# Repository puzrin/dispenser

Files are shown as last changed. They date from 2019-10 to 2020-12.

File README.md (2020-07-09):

SMT solder paste and flux dispenser
===================================




**WIP**

> Motorized dispenser for SMT boards soldering. Compact, cheap & easy to do.



Schematic & PCB:

- [EasyEDA project page](https://easyeda.com/puzrin/dispenser) - order PCB and
  all components in couple of clicks.

Project page on [hackaday.io](https://hackaday.io/project/166699-solder-paste-and-flux-dispenser).
See progress and other tips in build logs.

## Build & usage

- [Assembly guide](doc/assembly.md)
- [User manual](doc/manual.md)

If you plan to develop new features or create fixes - see
[Devolopment notes](doc/development.md).

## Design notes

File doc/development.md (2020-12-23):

Development notes<!-- omit in toc -->
=================

- [PC Simulator](#pc-simulator)
- [Messaging via USB Serial](#messaging-via-usb-serial)
- [Bare metal debug](#bare-metal-debug)

## PC Simulator

Firmware has simulator option for quick GUI development on desktop. It requires
SDL2 and was tested with Ubuntu 18.04LTS.

For dependencies install:

```sh
sudo apt-get install libsdl2-dev
```

To build & execute, via PlatformIO menu: `Terminal` -> `Run Build Task` ->
`PlatformIO: Execute (emulator)`.

## Messaging via USB Serial

Dispenser has built-in USB CDC descriptor with `stdout` retargeting. All
`printf()` output will be sent to virtual COM-port. By default, it sends
 LVGL memory pool usage info.

In linux, to see `tty` name of attached device type:

```sh
dmesg | grep tty
```

Then, to see messages, use:

```sh
screen /dev/<tty_name_from_dmesg>
```

For example: `screen /dev/ttyACM0`.

## Bare metal debug

In some cases you may wish to debug bare metal. PCB has SWD connector pins,
where to can attach ST-Link/V2. See PlatformIO docs for more details about
debugger.

We do not promote SWD connector in other documents, because for ordinary use USB
is enough and more simple.

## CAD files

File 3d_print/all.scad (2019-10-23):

e = 0.01;
2e = 0.02;

$fn = 128;

pcb_wide_w = 25;
pcb_wide_len = 40;
pcb_narrow_w = 15;
pcb_len = 120;

pcb_color = "Pink";


motor_dia = 15;
motor_len = 20;
motor_flange_len = 1; // shaft flange bearing outer
motor_shaft_len = 7;
motor_shaft_dia = 3;

motor_color = "RoyalBlue";

shaft_coupler_dia = 9;
shaft_coupler_len = 20;
shaft_coupler_offset = motor_len + motor_flange_len;

pusher_path_len = 35;

pusher_rod_len = pusher_path_len + 7;
pusher_rod_dia = 3;

pusher_len = pusher_path_len + 7;
pusher_dia = 11;

pusher_max_offset = motor_len + motor_flange_len + shaft_coupler_len + pusher_path_len + pusher_len;


////////////////////////////////////////////////////////////////////////////////
// Syringe sizes

s_medical_10cc = [
    20.4, // flange_h
    31.6, // flange_w
    16.5, // outer_dia
    14.5, // inner_dia
    75.3, // inner length
    6.5   // pusher head fatness
];

s_pneumo_10cc = [
    22.5, // flange_h
    34.1, // flange_w
    18.5, // outer_dia
    15.5,  // inner_dia
    75.3, // inner length
    2   // pusher head fatness
];

function s_flange_h(data) = data[0];
function s_flange_w(data) = data[1];
function s_outer_dia(data) = data[2];
function s_inner_dia(data) = data[3];
function s_body_len(data) = data[4];
function s_pusher_head(data) = data[5];
function s_axis_z(data) = s_flange_h(data) / 2;

function s_offset(data) = pusher_max_offset - s_body_len(data) + s_pusher_head(data);


////////////////////////////////////////////////////////////////////////////////
// Printed elements

module pusher() {
    //cylinder(pusher_len, d = pusher_dia);
    inner = 4/2 + 0.1;
    outer = pusher_dia/2;
    enforcer_h = 10;
    rounding = 0.5;
    gap_h = 15;
    
    f_ofs = 20;
    f_h = 3;
    
    //color("Red", 0.4)
    difference() {
        rotate_extrude()
        polygon([
            [ inner, 0 ],

            // stopper for metal enforcer insert
            [ inner, enforcer_h ],
            [ inner - 0.4, enforcer_h + 0.4 ],
            [ inner,  enforcer_h + 0.4 + 0.4 ],
        
            [ inner, pusher_len ],
            [ outer - rounding, pusher_len ],
            [ outer, pusher_len - rounding ],

            // Place for soft friction material
            [ outer, f_ofs +f_h + 0.5 ],
            [ outer - 0.5, f_ofs + f_h ],
            [ outer - 0.5, f_ofs ],
            [ outer, f_ofs - 0.5 ],


            [ outer, rounding ],
            [ outer - rounding, 0 ],
        ]);
        
        translate([ 0, 0, pusher_len - gap_h/2 + e ])
        cube([pusher_dia + e, 1, gap_h], center = true);

        rotate([ 0, 0, 90 ])
        translate([ 0, 0, pusher_len - gap_h/2 + e ])
        cube([pusher_dia + e, 1, gap_h], center = true);
    }
}

module motor_support(syringe) {
    space = (s_flange_h(syringe) - motor_dia) / 2;

    difference() {
        translate([ 0, -pcb_wide_w/2, 0 ])
        cube([ motor_len, pcb_wide_w, space * 2 ]);
        
        motor_body(syringe);
    }
}

module syringe_support(syringe) {
    space = (s_flange_h(syringe) - s_outer_dia(syringe)) / 2;
    support_len = 15;
    support_w = 10;

    difference() {
        translate([ 0, -support_w/2, 0 ])
        cube([support_len, support_w, space * 1.5]);
        
        translate([ -e, 0, s_flange_h(syringe)/2 ])
        rotate([0, 90, 0])
        cylinder(support_len + 2e,d = s_outer_dia(syringe));
    }
}

////////////////////////////////////////////////////////////////////////////////
// Virtual elements

module pcb() {
    smoothed_len = (pcb_wide_w - pcb_narrow_w) / 2;
    
    color(pcb_color, 0.5)
    translate([ 0, 0, -2 ])
    linear_extrude(1.6)
    difference() {
        polygon([
            [ 0, pcb_wide_w/2 ],
            [ pcb_wide_len, pcb_wide_w/2 ],
            [ pcb_wide_len + smoothed_len, pcb_narrow_w/2 ],
            [ pcb_len, pcb_narrow_w/2 ],
            [ pcb_len, -pcb_narrow_w/2 ],
            [ pcb_wide_len + smoothed_len, -pcb_narrow_w/2 ],
            [ pcb_wide_len, -pcb_wide_w/2 ],
            [ 0, -pcb_wide_w/2 ]    
        ]);
        
        translate([ 51, 0, 0 ]) {
            ofs = pcb_narrow_w / 2;

            translate([ 0, ofs, 0]) circle(d = 3);
            translate([ 0, -ofs, 0]) circle(d = 3);
            translate([ 6, ofs, 0]) circle(d = 3);
            translate([ 6, -ofs, 0]) circle(d = 3);
        }
    }
}


module motor_body(syringe) {
    z_level = s_axis_z(syringe);

    translate([ 0, 0, z_level])
    rotate([0, 90, 0])
    translate([ 0, 0, -e ])
    cylinder(motor_len + 2e, d = motor_dia);
}

module motor(syringe) {
    z_level = s_axis_z(syringe);

    color(motor_color, 0.6)
    motor_body(syringe);

    translate([ 0, 0, z_level])
    rotate([0, 90, 0]) {
        color(motor_color)
        cylinder(motor_len + motor_shaft_len, d = motor_shaft_dia);
    }
}


module pusher_model(syringe) {
    z_level = s_axis_z(syringe);
    
    translate([ shaft_coupler_offset, 0, z_level])
    rotate([0, 90, 0]) {
        // Coupling
        color("SeaGreen", 0.7)
        cylinder(shaft_coupler_len, d = shaft_coupler_dia);

        // Pusher shaft
        color(motor_color, 0.5)
        translate([ 0, 0, shaft_coupler_len/2 ])
        cylinder(pusher_rod_len + shaft_coupler_len/2, d = pusher_rod_dia);
        
        // Working body
        translate([ 0, 0, shaft_coupler_len + pusher_path_len ])
        pusher();
    }
}

module syringe_body(syringe) {
    h = s_body_len(syringe) + 1;
    z_level = s_axis_z(syringe);

    color("Azure", 0.4)
    translate([
        s_offset(syringe),
        0,
        z_level
    ])
    rotate([0, 90, 0])
    difference() {
        union() {
            cylinder(h, d = s_outer_dia(syringe));
            
            translate([ 0, 0, 0.5 ])
            cube([
                s_flange_h(syringe),
                s_flange_w(syringe),
                1
            ], center = true);
            
            translate([ 0, 0, h - e ]) {
                cylinder(9.5, d = 8);
                cylinder(11.5, d = 4);
            }
        };
        
        translate([ 0, 0, -e ])
        cylinder(h - 1, d = s_inner_dia(syringe));
    }
}

////////////////////////////////////////////////////////////////////////////////

syringe = s_medical_10cc;
//syringe = s_pneumo_10cc;

print = true;

if (print == false) {
    pcb();
    
    translate([ 0, 0, 1 ]) {
        motor(syringe);
        pusher_model(syringe);
        syringe_body(syringe);
    }

    motor_support(syringe);

    translate([ 52, 0, 0])
    syringe_support(syringe);

    translate([ 103, 0, 0])
    syringe_support(syringe);
} else {
    pusher();

    translate([ 10, 0, 0])
    motor_support(syringe);

    translate([ 35, 0, 0])
    syringe_support(syringe);

    translate([ 55, 0, 0])
    syringe_support(syringe);
}

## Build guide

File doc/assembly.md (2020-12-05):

Device assembly <!-- omit in toc -->
===============

- [Required components](#required-components)
- [PCB assembly](#pcb-assembly)
- [Firmware upload](#firmware-upload)
- [Motor & syringe mount](#motor--syringe-mount)
- [Needle caps](#needle-caps)
- [The end :)](#the-end-)

## Required components

This dispenser is inexpensive and small, expected to be used without syringe replace. Consider build separate one for each substance you plan to use (normal
paste, low temp paste, flux).

&nbsp; | Name | Comment
-----|-------------|--------
1 | [PCB & Components](https://easyeda.com/puzrin/dispenser) | Go to EasyEda project page and order both in couple of clicks. If you order PCB first, components second, then you will be able to join delivery and save some bucks. SMT stencil strongly advised, see note below.
2 | [0.96" IPS Display](https://www.aliexpress.com/item/32861823719.html) |
3 | [Micro stepper motor](https://www.aliexpress.com/item/32979960185.html) | Other motors will need rework of 3d-printed supports.
4 | [Gearbox 1:300+ with long shaft](https://www.aliexpress.com/item/32987637967.html) | For max gear ratio select lowest RPM.
5 | [PVC transparent heat shrink tube 23mm](https://aliexpress.ru/item/32787322976.html) | Display mount.
6 | [Double side foam tape, 15*1mm](https://www.aliexpress.com/item/33050888785.html) | Display mount.
6 | [22 AWG wire](https://www.aliexpress.com/item/32854919883.html) | SMT stencil positioning & motor/syringe supports mount.
7 | [Heat shrink tube 35mm](https://www.aliexpress.com/item/32791427710.html) | Motor mount / electronics protection.
8 | [Cable ties 150-200mm](https://www.aliexpress.com/item/32807062474.html) | Syringe mount. 100mm enough for all syringes except 10cc. Width 2.5-3.0mm.
9 | [Silicone heat shrink tube 0.8mm, 1.0mm, 1.5mm](https://atopelec.aliexpress.com/store/group/Silicone-Heat-Shrink-Tubing/118669_505069419.html) | Needle caps, inner layer.
10 | [Heat shrink tube 1:4 with glue, 4mm](https://www.aliexpress.com/item/32787521306.html) | Needle caps, outer layer.
11 | [Joysick cap, 2mm](https://www.aliexpress.com/item/4000005913318.html) | Optional, but recommended.
12 | [Syringes](https://www.aliexpress.com/item/32920861566.html) | 1cc recommended for soldering paste with max precision. 3cc - acceptable. 10cc - for fluxes when precision not critical, and for refill.
13 | [Needles](https://www.aliexpress.com/item/32256297497.html) | Needles choice from syringe set is too small. Buy separate set.
14 | [Micro USB silicon cable](https://www.aliexpress.com/item/32858516897.html) | Very soft cable strongly advised for convenience.

Note. You are strongly advised to order SMT stencil for your PCB. That will
add ~ 8$ in total to your order - good price for convenience. On placing stencil
order at jlcpcb, select option "custom size", and define 30*130mm. Then stencil
will be compact and light, with small delivery cost. You need top layer only. If
you order SMT stencil, add this comment:

_"Please make stencil with my paste layer directly. Make sure 2 TP rounds 0.7mm
with X = 43.0 and X = 108.0 exist"_

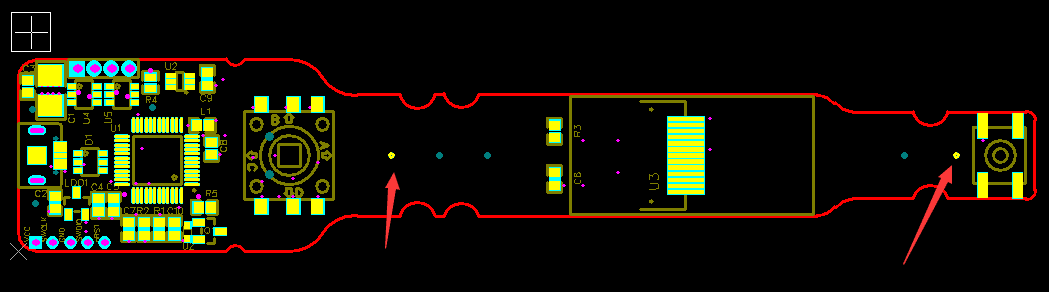
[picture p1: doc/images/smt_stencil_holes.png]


## PCB assembly

This sequence is for assembly with heat gun:

- Solder everything except buttons and LCD.
- Solder buttons manually.
- Wash PCB from flux.
- Solder LCD.
- Use IPA to accurately clean LCD soldering area. Or leave as is, if
  your flux is no-clean.

Warning. DON'T USE STRONG CLEANERS WITH LCD. It's not sealed, assembled with
soft glue and will be damaged. That's why it's better to install it in last
moment - you can clean PCB anyhow, but use IPA only with LCD.

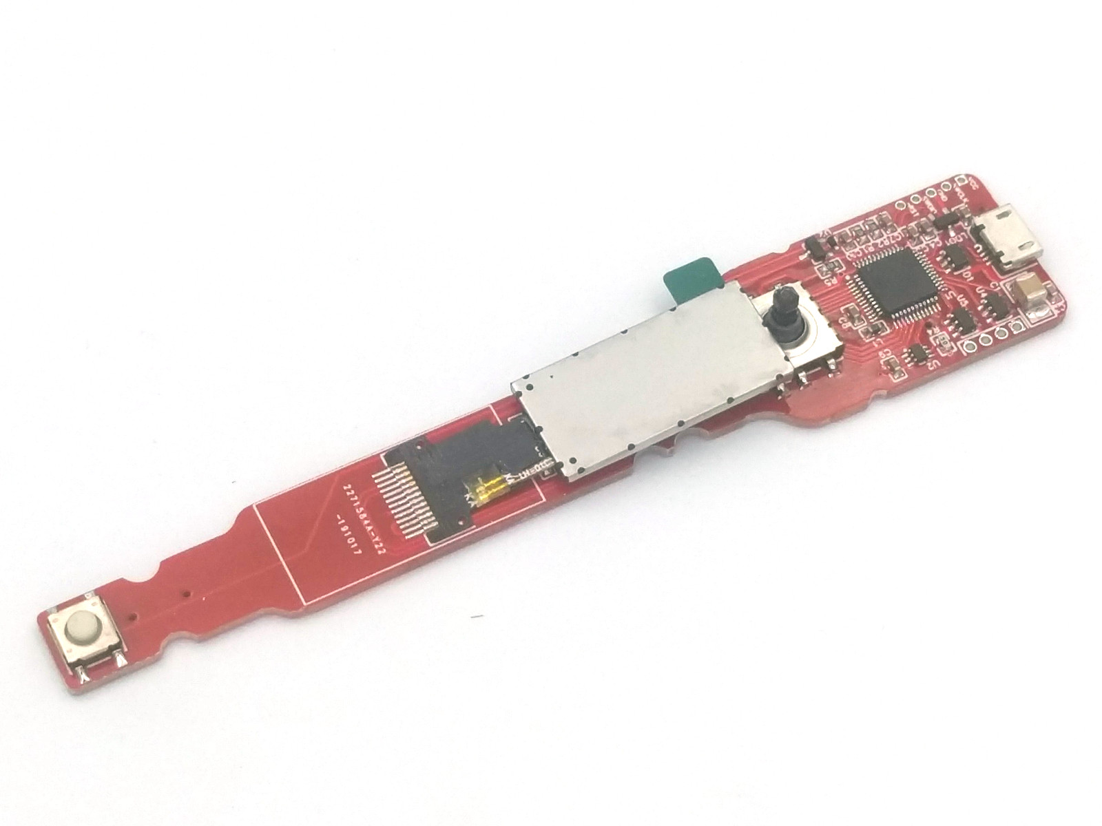
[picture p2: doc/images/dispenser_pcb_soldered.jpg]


Note. _Here it's good idea to upload firmware and check display works, prior to
continue (see instructions in next chapter)_.

Now mount LCD to PCB:

- Use double side foam tape. Stick to LCD first, then cut borders, then stick
  to PCB
- Fit heat shrink tube over that. You need 40mm of 23mm-wide tube. Center it
  over LCD, then shrink sides, front and back.

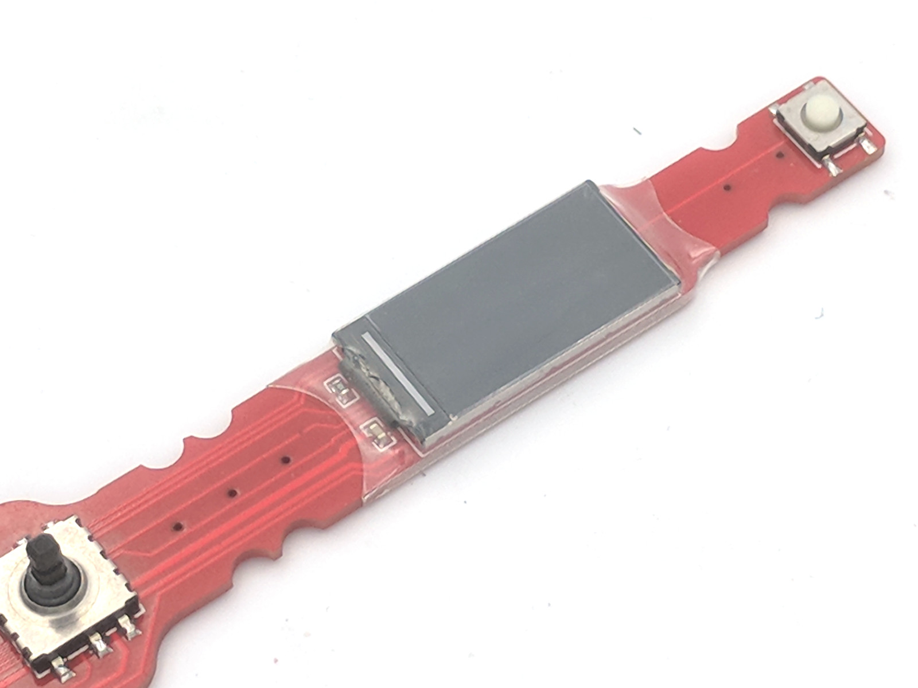
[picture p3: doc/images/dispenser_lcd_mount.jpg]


Don't worry about small air bubbles at screen surface, those will not affect
image quality anyhow. It's possible to use special UV-activated glue for
displays to avoid air gaps. But that does not worth efforts been spent.

Assembled PCB with power on:

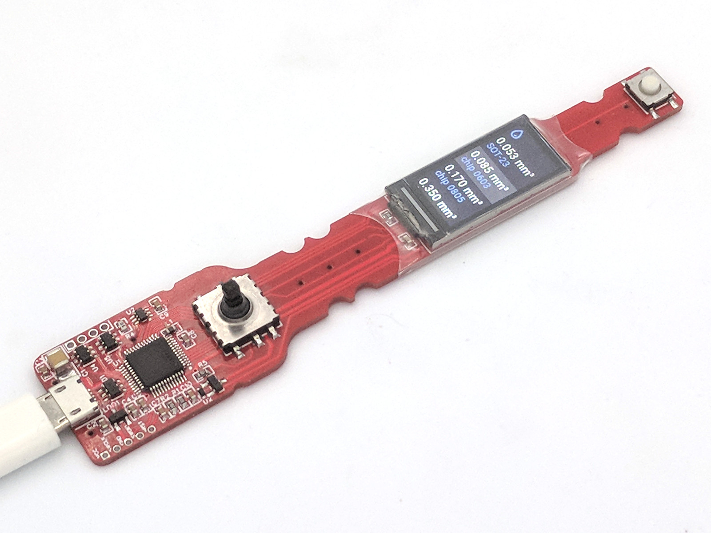
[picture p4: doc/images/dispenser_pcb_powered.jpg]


## Firmware upload

You need VS Code to build and upload firmware. It's our choice, because
it works on all operating systems and requires almost zero efforts to configure.

1. Install [VS Code](https://code.visualstudio.com/). Then configure hardware if
   needed:
   - For Linux, add [udev rules](http://docs.platformio.org/en/latest/installation.html#troubleshooting)
2. Clone this repo or download as zip archive and unpack somewhere.
3. Open folder in VS Code AND after it suggests to install plugins - agree
   with everything. That should install PlatformIO and all required dependencies.

How to flash:

1. Push joystick button and attach USB cable. It's important to push joystick
   before cable attached, to put device in programming mode.
2. In VS Code menu select `Terminal` -> `Run task` -> `PlatformIO: Upload (hardware_usb)`
   and wait until succeed.
3. Re-insert USB cable. You should see dispenser menu on display.

## Motor & syringe mount

TBD

## Needle caps

It's important to protect soldering paste from drying while not used. Here is
simple recipe of needle caps. You will need 2 heat shrink tubes:

- Small silicone tube. They have small shrink ratio (1.7:1 only), so buy several
  sizes to fit all 0.8/1.0/1.5mm.
- Bigger tube, 4mm, with glue layer & 1:4 ratio.

First, shrink 10mm of silicone tube at needle edge. Then shrink 15-20mm of
bigger tube and squeeze the end. Take off and cut the ends for accurate look.
See result:

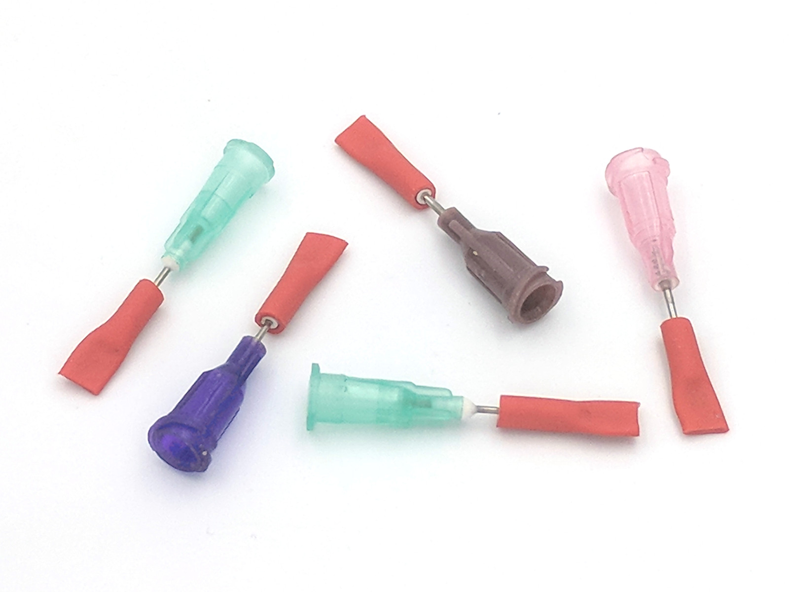
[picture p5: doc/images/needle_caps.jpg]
Needle caps


## The end :)

When dispenser ready, follow to [User Manual](./manual.md).

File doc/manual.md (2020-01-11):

User Manual <!-- omit in toc -->
===========

- [Control](#control)
- [Settings](#settings)
- [Viscosity](#viscosity)
- [Syringe refill](#syringe-refill)

Dispenser works in 2 modes - dose and flow. In dose, it dispense fixed portions
on each press. In flow mode, it continue dispense until button pressed.

Dose volume and dispense speed are selectable.

## Control

Joystick:

- Short push - mode switch (portion/flow).
- Long push - goto settings.
- Up/Down - move selection.
- Left/Right - change value (settings only).

You can edit `src/doses.cpp` file to change list of selectable portions.

## Settings

This params are used to estimate optimal dispense speed and portion volumes.

- **Syringe dia** - inner diameter of syringe. Required to properly calculate
  portion sizes. If you plan to dispense very small doses (0603 and below), we
  recommend to use smallest possible syringe (1cc).
- **Viscosity** - defines dispense speed and retract size. Typical values are
  described in next chapter.
- **Flux volume** - % of flux in paste. Needed to calculate proper volume of
  solder. If you need to dispence glues or fluxes - set to zero.
- **Fast move** - quick move pusher back and forward for syringe refill.

## Viscosity

Viscosity depend very much on temperature. Table below contain only average
value for room env.

_cP = centipoise = 0.1 Pa·s (pascal-second) = mPa·s_

Substance | Viscosity (cP)
----------|---------------
Soldering paste for SMT stencil | 650K-1200K
Soldering paste for dispenser | 300K-450K
Glycerol | 1400
Water | 1

## Syringe refill

Everything is done without disassembly. You will need only additional syringe
and luer coupler.

Notes:

- It's important to fill syringe without air bubbles.
- Avoid buy paste in syringes, because it can have air bubbles with very high
  probability. Prefer flasks.

Steps:

1. Fill helper (charger) syringe with paste. You can do that in different ways:
   - As on this video.
2. Move dispenser's pusher back via settings menu.
3. Attach needle to charger and fill dispenser's nozzle to leave no air.
4. Change needle to luer coupler and make sure i't filled with paste.
   Fill coupler before attach
5. Attach another end of coupler to dispenser and fill it.
6. Attach needle with protective cap to dispenser.

Tips:

- You can heat paste to 40-50C in hot water, to make it more liquid. But don't
  heat it too much and too long, because it can stratify.
- You can experiment with adding some flux to make old paste more liquid. But
  consider just buy paste in smaller packaging and use new one :). Paste is
  cheap, don't search difficulties to save couple of bucks.

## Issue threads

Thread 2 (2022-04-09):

Major bug in your source code!

heyrussia, 2022-04-09:
Привет @puzrin из StPetersburg.
Может быть, вы проснулись сегодня утром счастливым, как обычно, не особо задумываясь о жизни.
К сожалению, я должен лишить вас этого прекрасного дня.
Потому что вы были выбраны нами для великой задачи.

Украина уже больше месяца находится в состоянии войны.
Правительство России  вторглось в Украину, без согласия граждан. Ваши сыновья, мужья и просто знакомые погибают и становятся калеками, на войне, которая нужна лишь Путину.

**Но вы можете что-то изменить.**

Выполните следующие шаги, чтобы безопасно присоединиться к Сопротивлению и работать с другими, чтобы изменить историю к лучшему:

1. Установите бесплатный VPN-клиент на свой компьютер или смартфон.
2. Загрузите браузер Tor [https://www.torproject.org/](https://www.torproject.org/)
3. Присоединяйтесь к Матричному серверу Сопротивления. [https://matrix.to/#/#resistance-against-the-government:matrix.org](https://matrix.to/#/#resistance-against-the-government:matrix.org)
4. Найдите свои группы и организуйте сопротивление
5. Поделитесь этим сообщением со своими близкими друзьями и семьей или анонимно в Интернете.

---

Hello @puzrin from StPetersburg.

Maybe you woke up this morning happy as usual, without thinking much about life.
Unfortunately, I have to distract you from this beautiful day.
Because **you** have been chosen by us for a great task.

Ukraine has been at war for over a month.
The Russian government has invaded Ukraine without informing the citizens.
Your sons, husbands and just acquaintances are dying and becoming crippled in a war that only Putin needs.
Now everyone involved is suffering greatly from the consequences of this attack.

**But you can change something.**

Follow these steps to safely join the Resistance and work with others to change history for the better:

1. Install a free VPN client on your computer or smartphone.
2. Download the Tor Browser [https://www.torproject.org/](https://www.torproject.org/)
3. Join the Matrix Server of the Resistance [https://matrix.to/#/#resistance-against-the-government:matrix.org](https://matrix.to/#/#resistance-against-the-government:matrix.org)
4. Find your groups and organize the resistance
5. Share this message with your close friends and family or anonymously on the web

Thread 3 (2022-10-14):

Solder paste and flux dispenser

crazoff, 2022-10-14:
Здравствуйте Виталий. Заинтересовал паш проект https://hackaday.io/project/166699-solder-paste-and-flux-dispenser Решил повторить, но возникли трудности со скачиванием прошивки микроконтроллера. Я использовал Visual Studio Code, при заполнении которого выдается следующее сообщение.

* Выполнение задачи: C:\Users\Crazoff\.platformio\penv\Scripts\platformio.exe run --target upload

Предупреждение! Параметр конфигурации `src_build_flags` в разделе [env:emulator] устарел и будет удален в следующем выпуске! Вместо этого используйте `build_src_flags`
Предупреждение! Параметр конфигурации `src_filter` в разделе [env:emulator] устарел и будет удален в следующем выпуске! Вместо этого используйте `build_src_filter`
Предупреждение! Параметр конфигурации `src_filter` в разделе [env:hardware_stlink] устарел и будет удален в следующем выпуске! Вместо этого используйте `build_src_filter`
Эмулятор обработки (платформа: родная)
-------------------------------------------------- ------------------------------
Подробный режим можно включить с помощью опции `-v, --verbose`
LDF: поиск зависимостей библиотеки -> https://bit.ly/configure-pio-ldf
Режимы LDF: Finder ~ цепочка, Совместимость ~ soft
Диспетчер библиотек: установка библиотеки встроенных шаблонов @ ~18.3.2
Предупреждение! Не удалось найти пакет с требованиями «Встроенная библиотека шаблонов @ ~ 18.3.2» для вашей системы «windows_amd64».
Найдено 2 совместимые библиотеки
Сканирование зависимостей...
График зависимости
|-- лвгл @ 6.1.1
|-- lv_drivers @ 6.1.1
| |-- лвгл @ 6.1.1
Сборка в релизном режиме
Компиляция .pio\build\emulator\hal\sdl2\app_hal.o
"g++" \xad\xa5 \xef\xa5\xe2\xe1\xef \xa2\xad\xe3\xe2७\xad\xa5\xa9 \xa8\xab\xa8 \xa2\xad\xa5譥\xa9
\xaa\xae\xac\xa0\xad\xa4\xae\xa9, \xa8ᯮ\xab\xad塞\xae\xa9 \xafணࠬ\xac\xae\xa9 \xaa8\xab\xa8 \xaf\xa0\xaa\xa5 \xe2\xad\xeb\xac 䠩\xab\xae\xac.
Компиляция .pio\build\emulator\src\app.o
Компиляция .pio\build\emulator\src\doses.o
"g++" \xad\xa5 \xef\xa5\xe2\xe1\xef \xa2\xad\xe3\xe2७\xad\xa5\xa9 \xa8\xab\xa8 \xa2\xad\xa5譥\xa9
\xaa\xae\xac\xa0\xad\xa4\xae\xa9, \xa8ᯮ\xab\xad塞\xae\xa9 \xafணࠬ\xac\xae\xa9 \xaa8\xab\xa8 \xaf\xa0\xaa\xa5 \xe2\xad\xeb\xac 䠩\xab\xae\xac.
Компиляция .pio\build\emulator\src\fonts\my_font_icons_18.o
"g++" \xad\xa5 \xef\xa5\xe2\xe1\xef \xa2\xad\xe3\xe2७\xad\xa5\xa9 \xa8\xab\xa8 \xa2\xad\xa5譥\xa9
\xaa\xae\xac\xa0\xad\xa4\xae\xa9, \xa8ᯮ\xab\xad塞\xae\xa9 \xafணࠬ\xac\xae\xa9 \xaa8\xab\xa8 \xaf\xa0\xaa\xa5 \xe2\xad\xeb\xac 䠩\xab\xae\xac.
Компиляция .pio\build\emulator\src\fonts\my_font_roboto_12.o
"gcc" \xad\xa5 \xef\xa5\xe2\xe1\xef \xa2\xad\xe3\xe2७\xad\xa5\xa9 \xa8\xab\xa8 \xa2\xad\xa5譥\xa9
\xaa\xae\xac\xa0\xad\xa4\xae\xa9, \xa8ᯮ\xab\xad塞\xae\xa9 \xafணࠬ\xac\xae\xa9 \xaa8\xab\xa8 \xaf\xa0\xaa\xa5 \xe2\xad\xeb\xac 䠩\xab\xae\xac.
Компиляция .pio\build\emulator\src\fonts\my_font_roboto_14.o
"gcc" \xad\xa5 \xef\xa5\xe2\xe1\xef \xa2\xad\xe3\xe2७\xad\xa5\xa9 \xa8\xab\xa8 \xa2\xad\xa5譥\xa9
\xaa\xae\xac\xa0\xad\xa4\xae\xa9, \xa8ᯮ\xab\xad塞\xae\xa9 \xafணࠬ\xac\xae\xa9 \xaa8\xab\xa8 \xaf\xa0\xaa\xa5 \xe2\xad\xeb\xac 䠩\xab\xae\xac.
Компиляция .pio\build\emulator\src\fonts\my_font_roboto_num_18.o
"gcc" \xad\xa5 \xef\xa5\xe2\xe1\xef \xa2\xad\xe3\xe2७\xad\xa5\xa9 \xa8\xab\xa8 \xa2\xad\xa5譥\xa9
\xaa\xae\xac\xa0\xad\xa4\xae\xa9, \xa8ᯮ\xab\xad塞\xae\xa9 \xafணࠬ\xac\xae\xa9 \xaa8\xab\xa8 \xaf\xa0\xaa\xa5 \xe2\xad\xeb\xac 䠩\xab\xae\xac.
Компиляция .pio\build\emulator\src\screen_dose.o
"gcc" \xad\xa5 \xef\xa5\xe2\xe1\xef \xa2\xad\xe3\xe2७\xad\xa5\xa9 \xa8\xab\xa8 \xa2\xad\xa5譥\xa9
\xaa\xae\xac\xa0\xad\xa4\xae\xa9, \xa8ᯮ\xab\xad塞\xae\xa9 \xafணࠬ\xac\xae\xa9 \xaa8\xab\xa8 \xaf\xa0\xaa\xa5 \xe2\xad\xeb\xac 䠩\xab\xae\xac.
Компиляция .pio\build\emulator\src\screen_flow.o
"g++" \xad\xa5 \xef\xa5\xe2\xe1\xef \xa2\xad\xe3\xe2७\xad\xa5\xa9 \xa8\xab\xa8 \xa2\xad\xa5譥\xa9
\xaa\xae\xac\xa0\xad\xa4\xae\xa9, \xa8ᯮ\xab\xad塞\xae\xa9 \xafணࠬ\xac\xae\xa9 \xaa8\xab\xa8 \xaf\xa0\xaa\xa5 \xe2\xad\xeb\xac 䠩\xab\xae\xac.
Компиляция .pio\build\emulator\src\screen_settings.o
"g++" \xad\xa5 \xef\xa5\xe2\xe1\xef \xa2\xad\xe3\xe2७\xad\xa5\xa9 \xa8\xab\xa8 \xa2\xad\xa5譥\xa9
\xaa\xae\xac\xa0\xad\xa4\xae\xa9, \xa8ᯮ\xab\xad塞\xae\xa9 \xafணࠬ\xac\xae\xa9 \xaa8\xab\xa8 \xaf\xa0\xaa\xa5 \xe2\xad\xeb\xac 䠩\xab\xae\xac.
"g++" \xad\xa5 \xef\xa5\xe2\xe1\xef \xa2\xad\xe3\xe2७\xad\xa5\xa9 \xa8\xab\xa8 \xa2\xad\xa5譥\xa9
\xaa\xae\xac\xa0\xad\xa4\xae\xa9, \xa8ᯮ\xab\xad塞\xae\xa9 \xafணࠬ\xac\xae\xa9 \xaa8\xab\xa8 \xaf\xa0\xaa\xa5 \xe2\xad\xeb\xac 䠩\xab\xae\xac.
Компиляция .pio\build\emulator\libc67\lvgl\lv_core\lv_debug.o
Компиляция .pio\build\emulator\libc67\lvgl\lv_core\lv_disp.o
*** [.pio\build\emulator\hal\sdl2\app_hal.o] Ошибка 1
*** [.pio\build\emulator\src\app.o] Ошибка 1
*** [.pio\build\emulator\src\doses.o] Ошибка 1
*** [.pio\build\emulator\src\fonts\my_font_icons_18.o] Ошибка 1
*** [.pio\build\emulator\src\fonts\my_font_roboto_12.o] Ошибка 1
*** [.pio\build\emulator\src\fonts\my_font_roboto_14.o] Ошибка 1
*** [.pio\build\emulator\src\fonts\my_font_roboto_num_18.o] Ошибка 1
*** [.pio\build\emulator\src\screen_dose.o] Ошибка 1
*** [.pio\build\emulator\src\screen_flow.o] Ошибка 1
*** [.pio\build\emulator\src\screen_settings.o] Ошибка 1
"gcc" \xad\xa5 \xef\xa5\xe2\xe1\xef \xa2\xad\xe3\xe2७\xad\xa5\xa9 \xa8\xab\xa8 \xa2\xad\xa5譥\xa9
\xaa\xae\xac\xa0\xad\xa4\xae\xa9, \xa8ᯮ\xab\xad塞\xae\xa9 \xafணࠬ\xac\xae\xa9 \xaa8\xab\xa8 \xaf\xa0\xaa\xa5 \xe2\xad\xeb\xac 䠩\xab\xae\xac.
*** [.pio\build\emulator\libc67\lvgl\lv_core\lv_debug.o] Ошибка 1
"gcc" \xad\xa5 \xef\xa5\xe2\xe1\xef \xa2\xad\xe3\xe2७\xad\xa5\xa9 \xa8\xab\xa8 \xa2\xad\xa5譥\xa9
\xaa\xae\xac\xa0\xad\xa4\xae\xa9, \xa8ᯮ\xab\xad塞\xae\xa9 \xafணࠬ\xac\xae\xa9 \xaa8\xab\xa8 \xaf\xa0\xaa\xa5 \xe2\xad\xeb\xac 䠩\xab\xae\xac.
*** [.pio\build\emulator\libc67\lvgl\lv_core\lv_disp.o] Ошибка 1
========================== [FAILED] Заняло 4,17 секунды =================== ========

Продолжительность состояния окружающей среды
------------- -------- ------------
эмулятор ОШИБКА 00:00:04.174
==================== 1 сбой, 0 успешно в 00:00:04.174 =================== знак равно

* Терминальный процесс "C:\Users\Crazoff\.platformio\penv\Scripts\platformio.exe 'run', '--target', 'upload'" завершился кодом выхода: 1.
* Терминал будет повторно использоваться задачами, нажмите любую клавишу, чтобы закрыть его.

* Выполнение задачи: C:\Users\Crazoff\.platformio\penv\Scripts\platformio.exe run --target upload

Предупреждение! Параметр конфигурации `src_build_flags` в разделе [env:emulator] устарел и будет удален в следующем выпуске! Вместо этого используйте `build_src_flags`
Предупреждение! Параметр конфигурации `src_filter` в разделе [env:emulator] устарел и будет удален в следующем выпуске! Вместо этого используйте `build_src_filter`
Предупреждение! Параметр конфигурации `src_filter` в разделе [env:hardware_stlink] устарел и будет удален в следующем выпуске! Вместо этого используйте `build_src_filter`
Эмулятор обработки (платформа: родная)
-------------------------------------------------- ------------------------------
Подробный режим можно включить с помощью опции `-v, --verbose`
LDF: поиск зависимостей библиотеки -> https://bit.ly/configure-pio-ldf
Режимы LDF: Finder ~ цепочка, Совместимость ~ soft
Диспетчер библиотек: установка библиотеки встроенных шаблонов @ ~18.3.2
Предупреждение! Не удалось найти пакет с требованиями «Встроенная библиотека шаблонов @ ~ 18.3.2» для вашей системы «windows_amd64».
Найдено 2 совместимые библиотеки
Сканирование зависимостей...
График зависимости
|-- лвгл @ 6.1.1
|-- lv_drivers @ 6.1.1
| |-- лвгл @ 6.1.1
Сборка в релизном режиме
Компиляция .pio\build\emulator\hal\sdl2\app_hal.o
"g++" \xad\xa5 \xef\xa5\xe2\xe1\xef \xa2\xad\xe3\xe2७\xad\xa5\xa9 \xa8\xab\xa8 \xa2\xad\xa5譥\xa9
\xaa\xae\xac\xa0\xad\xa4\xae\xa9, \xa8ᯮ\xab\xad塞\xae\xa9 \xafணࠬ\xac\xae\xa9 \xaa8\xab\xa8 \xaf\xa0\xaa\xa5 \xe2\xad\xeb\xac 䠩\xab\xae\xac.
Компиляция .pio\build\emulator\src\app.o
Компиляция .pio\build\emulator\src\doses.o
"g++" \xad\xa5 \xef\xa5\xe2\xe1\xef \xa2\xad\xe3\xe2७\xad\xa5\xa9 \xa8\xab\xa8 \xa2\xad\xa5譥\xa9
\xaa\xae\xac\xa0\xad\xa4\xae\xa9, \xa8ᯮ\xab\xad塞\xae\xa9 \xafணࠬ\xac\xae\xa9 \xaa8\xab\xa8 \xaf\xa0\xaa\xa5 \xe2\xad\xeb\xac 䠩\xab\xae\xac.
Компиляция .pio\build\emulator\src\fonts\my_font_icons_18.o
"g++" \xad\xa5 \xef\xa5\xe2\xe1\xef \xa2\xad\xe3\xe2७\xad\xa5\xa9 \xa8\xab\xa8 \xa2\xad\xa5譥\xa9
\xaa\xae\xac\xa0\xad\xa4\xae\xa9, \xa8ᯮ\xab\xad塞\xae\xa9 \xafணࠬ\xac\xae\xa9 \xaa8\xab\xa8 \xaf\xa0\xaa\xa5 \xe2\xad\xeb\xac 䠩\xab\xae\xac.
Компиляция .pio\build\emulator\src\fonts\my_font_roboto_12.o
"gcc" \xad\xa5 \xef\xa5\xe2\xe1\xef \xa2\xad\xe3\xe2७\xad\xa5\xa9 \xa8\xab\xa8 \xa2\xad\xa5譥\xa9
\xaa\xae\xac\xa0\xad\xa4\xae\xa9, \xa8ᯮ\xab\xad塞\xae\xa9 \xafணࠬ\xac\xae\xa9 \xaa8\xab\xa8 \xaf\xa0\xaa\xa5 \xe2\xad\xeb\xac 䠩\xab\xae\xac.
Компиляция .pio\build\emulator\src\fonts\my_font_roboto_14.o
"gcc" \xad\xa5 \xef\xa5\xe2\xe1\xef \xa2\xad\xe3\xe2७\xad\xa5\xa9 \xa8\xab\xa8 \xa2\xad\xa5譥\xa9
\xaa\xae\xac\xa0\xad\xa4\xae\xa9, \xa8ᯮ\xab\xad塞\xae\xa9 \xafணࠬ\xac\xae\xa9 \xaa8\xab\xa8 \xaf\xa0\xaa\xa5 \xe2\xad\xeb\xac 䠩\xab\xae\xac.
Компиляция .pio\build\emulator\src\fonts\my_font_roboto_num_18.o
"gcc" \xad\xa5 \xef\xa5\xe2\xe1\xef \xa2\xad\xe3\xe2७\xad\xa5\xa9 \xa8\xab\xa8 \xa2\xad\xa5譥\xa9
\xaa\xae\xac\xa0\xad\xa4\xae\xa9, \xa8ᯮ\xab\xad塞\xae\xa9 \xafணࠬ\xac\xae\xa9 \xaa8\xab\xa8 \xaf\xa0\xaa\xa5 \xe2\xad\xeb\xac 䠩\xab\xae\xac.
Компиляция .pio\build\emulator\src\screen_dose.o
"gcc" \xad\xa5 \xef\xa5\xe2\xe1\xef \xa2\xad\xe3\xe2७\xad\xa5\xa9 \xa8\xab\xa8 \xa2\xad\xa5譥\xa9
\xaa\xae\xac\xa0\xad\xa4\xae\xa9, \xa8ᯮ\xab\xad塞\xae\xa9 \xafணࠬ\xac\xae\xa9 \xaa8\xab\xa8 \xaf\xa0\xaa\xa5 \xe2\xad\xeb\xac 䠩\xab\xae\xac.
"g++" \xad\xa5 \xef\xa5\xe2\xe1\xef \xa2\xad\xe3\xe2७\xad\xa5\xa9 \xa8\xab\xa8 \xa2\xad\xa5譥\xa9
Компиляция .pio\build\emulator\src\screen_flow.o
\xaa\xae\xac\xa0\xad\xa4\xae\xa9, \xa8ᯮ\xab\xad塞\xae\xa9 \xafணࠬ\xac\xae\xa9 \xaa8\xab\xa8 \xaf\xa0\xaa\xa5 \xe2\xad\xeb\xac 䠩\xab\xae\xac.
Компиляция .pio\build\emulator\src\screen_settings.o
"g++" \xad\xa5 \xef\xa5\xe2\xe1\xef \xa2\xad\xe3\xe2७\xad\xa5\xa9 \xa8\xab\xa8 \xa2\xad\xa5譥\xa9
\xaa\xae\xac\xa0\xad\xa4\xae\xa9, \xa8ᯮ\xab\xad塞\xae\xa9 \xafணࠬ\xac\xae\xa9 \xaa8\xab\xa8 \xaf\xa0\xaa\xa5 \xe2\xad\xeb\xac 䠩\xab\xae\xac.
"g++" \xad\xa5 \xef\xa5\xe2\xe1\xef \xa2\xad\xe3\xe2७\xad\xa5\xa9 \xa8\xab\xa8 \xa2\xad\xa5譥\xa9
\xaa\xae\xac\xa0\xad\xa4\xae\xa9, \xa8ᯮ\xab\xad塞\xae\xa9 \xafணࠬ\xac\xae\xa9 \xaa8\xab\xa8 \xaf\xa0\xaa\xa5 \xe2\xad\xeb\xac 䠩\xab\xae\xac.
Компиляция .pio\build\emulator\libc67\lvgl\lv_core\lv_debug.o
Компиляция .pio\build\emulator\libc67\lvgl\lv_core\lv_disp.o
*** [.pio\build\emulator\hal\sdl2\app_hal.o] Ошибка 1
*** [.pio\build\emulator\src\app.o] Ошибка 1
*** [.pio\build\emulator\src\doses.o] Ошибка 1
*** [.pio\build\emulator\src\fonts\my_font_icons_18.o] Ошибка 1
*** [.pio\build\emulator\src\fonts\my_font_roboto_12.o] Ошибка 1
*** [.pio\build\emulator\src\fonts\my_font_roboto_14.o] Ошибка 1
*** [.pio\build\emulator\src\fonts\my_font_roboto_num_18.o] Ошибка 1
*** [.pio\build\emulator\src\screen_dose.o] Ошибка 1
*** [.pio\build\emulator\src\screen_flow.o] Ошибка 1
*** [.pio\build\emulator\src\screen_settings.o] Ошибка 1
"gcc" \xad\xa5 \xef\xa5\xe2\xe1\xef \xa2\xad\xe3\xe2७\xad\xa5\xa9 \xa8\xab\xa8 \xa2\xad\xa5譥\xa9
\xaa\xae\xac\xa0\xad\xa4\xae\xa9, \xa8ᯮ\xab\xad塞\xae\xa9 \xafணࠬ\xac\xae\xa9 \xaa8\xab\xa8 \xaf\xa0\xaa\xa5 \xe2\xad\xeb\xac 䠩\xab\xae\xac.
*** [.pio\build\emulator\libc67\lvgl\lv_core\lv_debug.o] Ошибка 1
"gcc" \xad\xa5 \xef\xa5\xe2\xe1\xef \xa2\xad\xe3\xe2७\xad\xa5\xa9 \xa8\xab\xa8 \xa2\xad\xa5譥\xa9
\xaa\xae\xac\xa0\xad\xa4\xae\xa9, \xa8ᯮ\xab\xad塞\xae\xa9 \xafணࠬ\xac\xae\xa9 \xaa8\xab\xa8 \xaf\xa0\xaa\xa5 \xe2\xad\xeb\xac 䠩\xab\xae\xac.
*** [.pio\build\emulator\libc67\lvgl\lv_core\lv_disp.o] Ошибка 1
========================== [FAILED] Заняло 3,06 секунды =================== ========
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

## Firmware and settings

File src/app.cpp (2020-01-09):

#include "app.h"
#include "app_hal.h"
#include "screen_dose.h"
#include "screen_flow.h"
#include "screen_settings.h"
#include"doses.h"
#include "lvgl.h"
#include "etl/cyclic_value.h"

#include "eeprom_emu.h"
#include "eeprom_flash_driver.h"
#include "stepper_control.h"

//#include <stdio.h>
#include "fonts_custom.h"

EepromEmu<EepromFlashDriver> eeprom;
app_data_t app_data;

StepperPwmParams pwm_params;
StepperControl<hal::StepperIO> stepper_control(&pwm_params);

// eeprom map
enum {
    ADDR_NEEDLE_DIA = 0,
    ADDR_SYRINGE_DIA = 1,
    ADDR_VISCOSITY = 2,
    ADDR_FLUX_PERCENT = 3,
    ADDR_DOSE_VOLUME = 4,
    ADDR_SPEED_SCALE = 5,
    ADDR_FLOW_MODE = 6,
    ADDR_LCD_BRIGHTNESS = 7
};


static void load_settings()
{
    app_data.needle_dia     = eeprom.read_float(ADDR_NEEDLE_DIA, 0.5f);
    app_data.syringe_dia    = eeprom.read_float(ADDR_SYRINGE_DIA, 15.0f);
    app_data.viscosity      = eeprom.read_float(ADDR_VISCOSITY, 1.0);
    app_data.flux_percent   = eeprom.read_float(ADDR_FLUX_PERCENT, 10.0f);
    app_data.dose_volume    = eeprom.read_float(ADDR_DOSE_VOLUME, doses[0].volume);
    app_data.speed_scale    = eeprom.read_float(ADDR_SPEED_SCALE, 1.0f);
    app_data.flow_mode      = (bool)eeprom.read_u32(ADDR_FLOW_MODE, 0);
    app_data.lcd_brightness = (uint8_t)eeprom.read_u32(ADDR_LCD_BRIGHTNESS, 100);
}

static void save_settings()
{
    eeprom.write_float(ADDR_NEEDLE_DIA, app_data.needle_dia);
    eeprom.write_float(ADDR_SYRINGE_DIA, app_data.syringe_dia);
    eeprom.write_float(ADDR_VISCOSITY,app_data.viscosity);
    eeprom.write_float(ADDR_FLUX_PERCENT, app_data.flux_percent);
    eeprom.write_float(ADDR_DOSE_VOLUME, app_data.dose_volume);
    eeprom.write_float(ADDR_SPEED_SCALE, app_data.speed_scale);
    eeprom.write_u32(ADDR_FLOW_MODE, (uint32_t)app_data.flow_mode);
    eeprom.write_u32(ADDR_LCD_BRIGHTNESS, app_data.lcd_brightness);
}


static bool saver_has_data = false;

static void saver_task(lv_task_t * task)
{
    if (!saver_has_data) return;
    saver_has_data = false;
    save_settings();

    (void)task;
}

// Save config to eeprom, but wait 1s of inactivity first
static void save_settings_debounced()
{
    static lv_task_t * task = lv_task_create(saver_task, 1000, LV_TASK_PRIO_LOWEST, NULL);

    lv_task_reset(task); // Start counting timeout from zero
    saver_has_data = true;
}

// Called after any settings update. Recalculate motor params and store
// state in "eeprom"
void app_update_settings()
{
    save_settings_debounced();
}


static void (*prev_screen_destroy)() = NULL;

void app_screen_create(bool to_settings)
{
    if (prev_screen_destroy) (*prev_screen_destroy)();

    if (to_settings)
    {
        prev_screen_destroy = &screen_settings_destroy;
        screen_settings_create();
        return;
    }

    if (app_data.flow_mode)
    {
        prev_screen_destroy = &screen_flow_destroy;
        screen_flow_create();
    }
    else {
        prev_screen_destroy = &screen_dose_destroy;
        screen_dose_create();
    }
}

void app_mode_switch()
{
    app_data.flow_mode = !app_data.flow_mode;
    app_update_settings();
    app_screen_create(false);
}


static void create_styles()
{
    lv_style_t * s;

    s = &app_data.styles.main;
    lv_style_copy(s, &lv_style_pretty);
    s->body.main_color = LV_COLOR_BLACK;
    s->body.grad_color = LV_COLOR_BLACK;
    s->body.radius = 0;
    s->body.border.width = 0;
    s->body.padding.bottom = 0;
    s->body.padding.left = 0;
    s->body.padding.right = 0;
    s->body.padding.top = 0;
    s->body.padding.inner = 0;
    s->text.color = LV_COLOR_WHITE;
    s->text.font = &my_font_roboto_14;

    s = &app_data.styles.list;
    lv_style_copy(s, &app_data.styles.main);
    s->body.padding.inner = 1;

    s = &app_data.styles.list_item;
    lv_style_copy(s, &app_data.styles.main);
    //s->body.padding.bottom = 10;

    s = &app_data.styles.list_title;
    lv_style_copy(s, &app_data.styles.main);
    s->text.font = &my_font_roboto_14;

    s = &app_data.styles.list_desc;
    lv_style_copy(s, &app_data.styles.main);
    s->text.font = &my_font_roboto_12;
    s->text.color = COLOR_SECONDARY;

    s = &app_data.styles.header_icon;
    lv_style_copy(s, &app_data.styles.main);
    s->text.font = &my_font_icons_18;
    s->text.color = COLOR_SECONDARY;

    s = &app_data.styles.flow_num;
    lv_style_copy(s, &app_data.styles.main);
    s->text.font = &my_font_roboto_num_18;
    s->text.color = COLOR_SECONDARY;
}


static void dispence_btn_scan_task(lv_task_t * task)
{
    static bool prev_pressed = false;
    static bool prev_press_mode_flow = false;

    if (!prev_pressed)
    {
        if (hal::key_start_on())
        {
            prev_pressed = true;
            prev_press_mode_flow = app_data.flow_mode;

            if (app_data.flow_mode) stepper_control.flow();
            else stepper_control.dose();
        }
    }
    else
    {
        if (!hal::key_start_on())
        {
            prev_pressed = false;
            if (prev_press_mode_flow) stepper_control.stop();
        }
    }

    (void)task;
}


static void hires_tick_handler()
{
    stepper_control.tick();

    static etl::cyclic_value<uint8_t, 0, 99> brightness_count;

    if (++brightness_count < app_data.lcd_brightness) hal::backlight(true);
    else hal::backlight(false);
}


int main()
{
    lv_init();
    hal::setup();
    hal::backlight(true);
    load_settings();

    create_styles();
    lv_obj_set_style(lv_scr_act(), &app_data.styles.main);

    app_data.group = lv_group_create();
    lv_indev_set_group(app_data.kbd, app_data.group);
    lv_group_set_wrap(app_data.group, false);

    app_data.screen_dose_scroll_pos = INT16_MAX;
    app_data.screen_flow_scroll_pos = INT16_MAX;
    app_data.screen_settings_scroll_pos = INT16_MAX;
    app_data.screen_settings_selected_id = -1;
    app_data.skip_key_enter_release = false;

    app_screen_create(false);

    hal::set_hires_timer_cb(hires_tick_handler);
    lv_task_create(dispence_btn_scan_task, 30, LV_TASK_PRIO_HIGH, NULL);

    hal::loop();
}

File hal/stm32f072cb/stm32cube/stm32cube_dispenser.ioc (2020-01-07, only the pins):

Mcu.UserName=STM32F072CBTx
PA11.Signal=USB_DM
PA12.Signal=USB_DP
PA13.Signal=SYS_SWDIO
PA14.Signal=SYS_SWCLK
PA2.Signal=GPIO_Output
PA3.Signal=GPIO_Output
PA4.Signal=SPI1_NSS
PA5.Signal=SPI1_SCK
PA7.Signal=SPI1_MOSI
PB1.Signal=ADC_IN9
PB12.Signal=GPIO_Output
PB13.Signal=GPIO_Output
PB14.Signal=GPIO_Output
PB15.Signal=GPIO_Output
PB8.Signal=GPIO_Input
PB9.Signal=GPIO_Output
PC13.Signal=GPIO_Input
PC14-OSC32_IN.Signal=GPIO_Input
PC15-OSC32_OUT.Signal=GPIO_Input
PF0-OSC_IN.Signal=GPIO_Input
PF1-OSC_OUT.Signal=GPIO_Input

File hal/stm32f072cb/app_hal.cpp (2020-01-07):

#include "app.h"
#include "app_hal.h"
#include "etl/debounce.h"

#include "main.h"
#include "adc.h"
#include "spi.h"
#include "tim.h"
#include "gpio.h"
#include "dma.h"

#include "lvgl.h"
#include "st7735.h"
#include "stdio_retarget.h"

extern "C" void SystemClock_Config(void);

#if MEM_USE_LOG != 0
#include "stdio.h"
static void sysmon_task(lv_task_t * param)
{
    (void) param;

    uint8_t mem_used_pct = 0;
    lv_mem_monitor_t mem_mon;
    lv_mem_monitor(&mem_mon);
    mem_used_pct = mem_mon.used_pct;

    printf(
        "[Memory] total: %d bytes, free: %d bytes, use: %d%% (%d)\r\n",
        (int)mem_mon.total_size,
        (int)mem_mon.free_size,
        (int)mem_used_pct,
        (int)(mem_mon.total_size - mem_mon.free_size)
    );
}
#endif

namespace hal {

// Key debouncers, protect from jitter
static etl::debounce<3> key_up, key_down, key_left, key_right, key_enter, key_start;

static uint32_t kbd_last_key = 0;
static lv_indev_state_t kbd_last_state;

static lv_disp_drv_t disp_drv;

// Scan keys every 10ms.
static void key_scan_task(lv_task_t * task)
{
        // Forwars button pins to debouncers
        key_down.add(HAL_GPIO_ReadPin(GPIOC, GPIO_PIN_13));
        key_up.add(HAL_GPIO_ReadPin(GPIOC, GPIO_PIN_15));
        key_right.add(HAL_GPIO_ReadPin(GPIOC, GPIO_PIN_14));
        key_left.add(HAL_GPIO_ReadPin(GPIOF, GPIO_PIN_0));
        key_enter.add(HAL_GPIO_ReadPin(GPIOF, GPIO_PIN_1));
        key_start.add(HAL_GPIO_ReadPin(GPIOB, GPIO_PIN_8));

        // Record data for indev reader the same way as in emulator.
        // In theory, events should be queued, but currently LVGL allows only.
        // single press/release event at each moment.
        if (key_up.has_changed())
        {
            if (key_up.is_set()) { kbd_last_key = LV_KEY_UP; kbd_last_state = LV_INDEV_STATE_PR; }
            else kbd_last_state = LV_INDEV_STATE_REL;
        }
        if (key_left.has_changed())
        {
            if (key_left.is_set()) { kbd_last_key = LV_KEY_LEFT; kbd_last_state = LV_INDEV_STATE_PR; }
            else kbd_last_state = LV_INDEV_STATE_REL;
        }
        if (key_down.has_changed())
        {
            if (key_down.is_set()) { kbd_last_key = LV_KEY_DOWN; kbd_last_state = LV_INDEV_STATE_PR; }
            else kbd_last_state = LV_INDEV_STATE_REL;
        }
        if (key_right.has_changed())
        {
            if (key_right.is_set()) { kbd_last_key = LV_KEY_RIGHT; kbd_last_state = LV_INDEV_STATE_PR; }
            else kbd_last_state = LV_INDEV_STATE_REL;
        }
        if (key_enter.has_changed())
        {
            if (key_enter.is_set()) { kbd_last_key = LV_KEY_ENTER; kbd_last_state = LV_INDEV_STATE_PR; }
            else kbd_last_state = LV_INDEV_STATE_REL;
        }
}

static bool my_keyboard_read(lv_indev_drv_t * indev_drv, lv_indev_data_t * data)
{
    static int prev_state;
    // Load prepared data
    data->state = kbd_last_state;
    data->key = kbd_last_key;

    //---------------------------------------------------------
    // HACK! Send release codes to group, to compensate lack of
    // existing ones
    //---------------------------------------------------------
    if (app_data.group)
    {
        // Spy data & inject events before continue
        if (data->state == LV_INDEV_STATE_REL && prev_state == LV_INDEV_STATE_PR)
        {
            lv_obj_t * selected = lv_group_get_focused(app_data.group);
            if (selected)
            {
                lv_event_send(selected, HACK_EVENT_RELEASED, &data->key);
            }
        }
    }

    prev_state = data->state;

    return false;
}

// State of "dispense" key.
bool key_start_on()
{
    return key_start.is_set();
}


//
// HiRes timer to create software PWM-s.
//

static void (*hires_timer_cb)(void) = NULL;

void set_hires_timer_cb(void (*handler)(void))
{
    hires_timer_cb = handler;
}


void setup(void)
{
    HAL_Init();
    SystemClock_Config();

    MX_GPIO_Init();
    MX_DMA_Init();
    MX_SPI1_Init();

    // Attach display buffer and display driver
    static lv_disp_buf_t disp_buf;
    static lv_color_t buf[LV_HOR_RES_MAX * 20];
    lv_disp_buf_init(&disp_buf, buf, NULL, LV_HOR_RES_MAX * 20);

    lv_disp_drv_init(&disp_drv);

    disp_drv.flush_cb = ST7735_flush_cb;
    disp_drv.buffer = &disp_buf;

    ST7735_Init(&hspi1, &disp_drv);

    lv_disp_drv_register(&disp_drv);

    //
    // Init keyboard
    //

    lv_indev_drv_t indev_drv;
    lv_indev_drv_init(&indev_drv);
    indev_drv.type = LV_INDEV_TYPE_KEYPAD;
    indev_drv.read_cb = my_keyboard_read;

    app_data.kbd = lv_indev_drv_register(&indev_drv);
    lv_task_create(key_scan_task, 10, LV_TASK_PRIO_HIGHEST, NULL);

    MX_ADC_Init();
    MX_TIM7_Init();
    MX_TIM6_Init();

    stdio_retarget_init();

    #if MEM_USE_LOG != 0
        lv_task_create(sysmon_task, 500, LV_TASK_PRIO_LOW, NULL);
    #endif

    HAL_TIM_Base_Start_IT(&htim6);
    HAL_TIM_Base_Start_IT(&htim7);
}

//
// Main loop
//

void loop(void)
{
    uint32_t tick_start = HAL_GetTick();

    while(1) {
        uint32_t tick_current = HAL_GetTick();

        if (tick_current - tick_start >= 5)
        {
            // Call ~ every 5ms
            tick_start = tick_current;
        	lv_task_handler();
        }
    }
}


//
// Set motor pins according to desired position. Everithing else
// done in software
//
// 0, 1, 2, 3 - respond to desired rotor position in full step wave mode
//

void StepperIO::to(uint16_t phase)
{
    off(); // clrear previous

    switch (phase & 0x3)
    {
        case 0:
            HAL_GPIO_WritePin(GPIOB, GPIO_PIN_14, GPIO_PIN_SET);
            break;
        case 1:
            HAL_GPIO_WritePin(GPIOB, GPIO_PIN_12, GPIO_PIN_SET);
            break;
        case 2:
            HAL_GPIO_WritePin(GPIOB, GPIO_PIN_15, GPIO_PIN_SET);
            break;
        case 3:
            HAL_GPIO_WritePin(GPIOB, GPIO_PIN_13, GPIO_PIN_SET);
            break;
    }
}

void StepperIO::off()
{
    HAL_GPIO_WritePin(
        GPIOB,
        GPIO_PIN_12 | GPIO_PIN_13 | GPIO_PIN_14 | GPIO_PIN_15,
        GPIO_PIN_RESET
    );
}


// Enable/Disable LCD backlight
void backlight(bool on)
{
    HAL_GPIO_WritePin(GPIOB, GPIO_PIN_9, on ? GPIO_PIN_SET : GPIO_PIN_RESET);
}


} // namespace

void HAL_TIM_PeriodElapsedCallback(TIM_HandleTypeDef *htim)
{
    if (htim->Instance == TIM7)
    {
        // HiRes (100 uS) timer
        if (hal::hires_timer_cb) hal::hires_timer_cb();
    }
    else if (htim->Instance == TIM6)
    {
        // 1 mS timer
        lv_tick_inc(1);
    }
}

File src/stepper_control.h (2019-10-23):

#ifndef __STEPPER_CONTROL__
#define __STEPPER_CONTROL__

#include "stepper.h"
#include "etl/cyclic_value.h"

// Use instead of "cyclic_value" when borders can be updated on the fly
#define INC_BY_MOD(X, Y) if ((++X) >= (Y)) X = 0;

template <typename STEPPER_IO>
class StepperControl
{
    Stepper<STEPPER_IO> stepper;

    enum State {
        STATE_STOPPED,

        STATE_FAST_FORWARD,
        STATE_FAST_BACK,

        STATE_FLOW_UNRETRACT,
        STATE_FLOW,
        STATE_FLOW_RETRACT,

        STATE_DOSE_UNRETRACT,
        STATE_DOSE,
        STATE_DOSE_RETRACT

    } state = STATE_STOPPED;

    enum Cmd {
        CMD_NONE = 0,
        CMD_FAST_FORWARD,
        CMD_FAST_BACK,
        CMD_FLOW,
        CMD_DOSE,
        CMD_STOP,
    };

    volatile Cmd pending_cmd = CMD_NONE;
    uint16_t ticks_count = 0;
    uint16_t steps_count = 0;
    uint16_t dose_count = 0;

    void to_state(State new_state)
    {
        ticks_count = 0;
        steps_count = 0;
        state = new_state;
    }

    void step_next()
    {
        current_stepper_phase++;
        stepper.go(current_stepper_phase);
    }

    void step_prev()
    {
        current_stepper_phase++;
        stepper.go(current_stepper_phase);
    }

    void off()
    {
        // Do not disable motor power. Use stepper's "idle" feature, to reduce
        // current but keep motor position with little effort.
        // If full disable needed - uncomment line below.

        // stepper.off()
    }

    void process_commands()
    {
        switch (pending_cmd)
        {
        case CMD_FAST_FORWARD:
            // Switch immediately from any state
            to_state(STATE_FAST_FORWARD);
            break;

        case CMD_FAST_BACK:
            // Switch immediately from any state
            to_state(STATE_FAST_BACK);
            break;

        case CMD_STOP:
            switch (state)
            {
            case STATE_FAST_FORWARD:
            case STATE_FAST_BACK:
                to_state(STATE_STOPPED);
                break;

            case STATE_FLOW:
                to_state(STATE_FLOW_RETRACT);
                break;

            case STATE_FLOW_UNRETRACT:
            case STATE_FLOW_RETRACT:
                // Ignore until state ended
                return;

            // Other combinations should never happen
            default:
                off();
                to_state(STATE_STOPPED);
                break;
            }
            break;

        case CMD_FLOW:
            switch (state)
            {
            case STATE_STOPPED:
                to_state(STATE_FLOW_UNRETRACT);
                break;

            case STATE_FLOW:
            case STATE_FLOW_UNRETRACT:
                break;

            case STATE_FLOW_RETRACT:
                return;

            case STATE_DOSE:
                // Jump to flow directly, skip retracts
                to_state(STATE_FLOW);
                break;

            case STATE_DOSE_UNRETRACT:
            case STATE_DOSE_RETRACT:
                // Ignore until state ended
                return;

            // Other combinations should never happen
            default:
                off();
                to_state(STATE_STOPPED);
                break;
            }
            break;

        case CMD_DOSE:
            switch (state)
            {
            case STATE_STOPPED:
                to_state(STATE_DOSE_UNRETRACT);
                dose_count = dose_steps;
                break;

            case STATE_DOSE:
            case STATE_DOSE_UNRETRACT:
                // I receive one more request while in this state,
                // just increase dose size without interrupting process.
                dose_count += dose_steps;
                break;

            case STATE_DOSE_RETRACT:
                // Ignore until state ended
                return;

            case STATE_FLOW:
                // Jump to dose directly, skip retracts
                to_state(STATE_FLOW);
                dose_count = dose_steps;
                break;

            case STATE_FLOW_UNRETRACT:
            case STATE_FLOW_RETRACT:
                // Ignore until state ended
                return;

            // Other combinations should never happen
            default:
                off();
                to_state(STATE_STOPPED);
                break;
            }
            break;

        default:
            // This should never happen
            off();
            to_state(STATE_STOPPED);
            break;
        }

        pending_cmd = CMD_NONE;
    }

public:

    StepperControl(StepperPwmParams * _params) : stepper(_params) {}

    //
    // This variables should be initialised & updated externally,
    // according to config
    //

    // Defines rotation speed. Length of 1 step in 0.1us/sec
    uint16_t flow_pulse_period = 50;
    uint16_t retract_pulse_period = 20;

    // Current motor position, to calculate next one.
    etl::cyclic_value<uint8_t, 0, 3>  current_stepper_phase;

    // Dose size, in motor steps
    uint16_t dose_steps = 10;
    uint16_t retract_steps = 2;

    //
    // Public api
    //

    void flow() { pending_cmd = CMD_FLOW; };
    void stop() { pending_cmd = CMD_STOP; };
    void fast_forward() { pending_cmd = CMD_FAST_FORWARD; };
    void fast_back() { pending_cmd = CMD_FAST_BACK; };
    void dose() { pending_cmd = CMD_DOSE; };

    void tick() {
        process_commands();

        switch (state)
        {
        case STATE_FAST_FORWARD:
            if (ticks_count == 0) step_next();

            INC_BY_MOD(ticks_count, retract_pulse_period);
            break;

        case STATE_FAST_BACK:
            if (ticks_count == 0) step_prev();

            INC_BY_MOD(ticks_count, retract_pulse_period);
            break;

        case STATE_FLOW_UNRETRACT:
            if (ticks_count == 0) {
                if (++steps_count > retract_steps)
                {
                    to_state(STATE_FLOW);
                    break;
                }
                step_next();
            }
            INC_BY_MOD(ticks_count, retract_pulse_period);
            break;

        case STATE_FLOW:
            if (ticks_count == 0) step_next();

            INC_BY_MOD(ticks_count, flow_pulse_period);
            break;

        case STATE_FLOW_RETRACT:
            if (ticks_count == 0) {
                if (++steps_count > retract_steps)
                {
                    to_state(STATE_STOPPED);
                    break;
                }
                step_prev();
            }
            INC_BY_MOD(ticks_count, retract_pulse_period);
            break;
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

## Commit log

2019-12-23 cube config update: configure spi & dma
2019-12-24 add ST7735 display driver
2019-12-25 revive board buttons
2020-01-07 regenerate cubemx files: new firmware + full driver sources
2020-01-09 eeprom emulator fixes: avoid flags override and simplify logic
    [eeprom_emu.h]
2020-01-09 updated stm32 platform & added cubemx dir notes
2020-02-10 doc: use PVC heat shrink tube for display
2020-02-10 doc: use silicone tubes for needle caps
2020-07-09 CI: switch from travis o github actions
